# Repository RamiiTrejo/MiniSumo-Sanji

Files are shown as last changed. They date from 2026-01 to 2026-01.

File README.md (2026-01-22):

# MiniSumo-Sanji
Minisumo

 ## PLaca de Sanji
  Sanji contará con una placa hecha medida la cual puede ser alimentada con baterias de 2s-3s (LiPo), Con un microcontrolador ESP32 Embebido posee la capacidad de llevar 7 sensores, 5 de distancia y 2 de piso, con Divisores de tension en caso de trabajar con 5v, posee drivers TA6586 los cuales pueden llegar a soportar 5A de corriente pico por cada motor, tiene la opcion de agregar Pantalla Oled de 0.91 de Preferencia, ServoMotor para utilizarlo con Banderas, y Modulo de Inicio IR de Arsumo, 2 Botones de Manejo, 2 para poder cargar Programas al ESP32, y 3 Leds indicadores en caso de no querer utilizar un Display

<div align="center">
<br>
 <strong>FRONT VIEW</strong>
</div> 

<div align="center">
 <br>
 <strong>BACK VIEW</strong>
</div> 

 # 3D Sanji
minisumo v1
LATERAL MINISUMO
BACK MINISUMO

cómo se aprecia en kas imágenes, Sanji Llevara de momento 4 sensores JS40F De arsumo, también poseerá 1 par de ruedas JS2622, 2 sensores de línea QRE1113, y de momento par de Motores pololu N20 de 500RPM

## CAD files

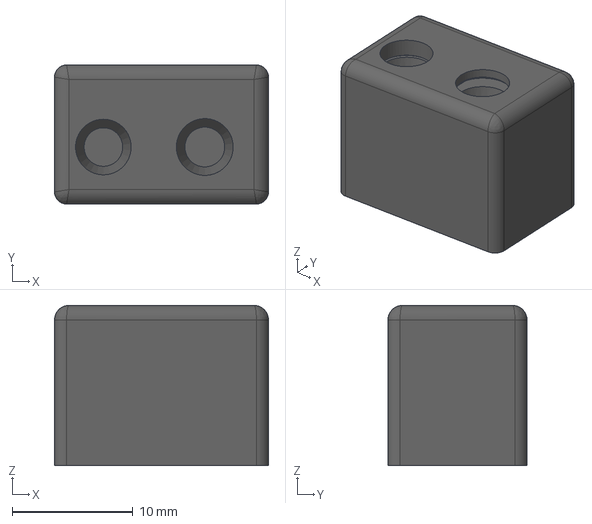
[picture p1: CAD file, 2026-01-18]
3D FILES SANJI/js40f-cad-step-jsumo.stp
17.7 x 11.5 x 13.3 mm

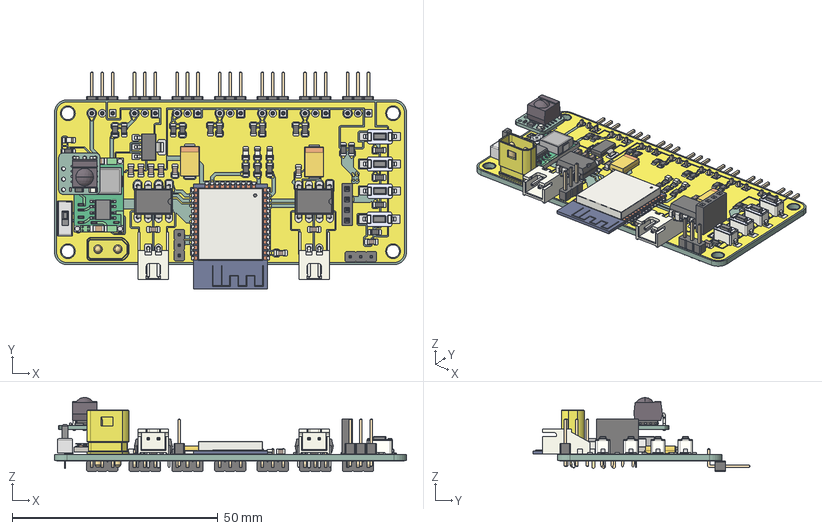
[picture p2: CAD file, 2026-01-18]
3D FILES SANJI/Sanji V1.step
85.5 x 52.7 x 18.0 mm
R_0805_2012Metric x 20
LED_0805_2012Metric x 4
PCB
C_0805_2012Metric x 10
DIP-8_W7.62mm x 2
XT30AW-M
SOT-223
JST_XH_S2B-XH-A-1_1x02_P2.50mm_Horizontal x 2
RS-032G05A3-SMRT x 4
PinHeader_1x03_P2.54mm_Vertical x 2
PinSocket_1x04_P2.54mm_Vertical
Mini360
ESP32-WROOM-32
SW_Slide-03_P2.54
CP_EIA-7343-20_Kemet-V x 2
PinHeader_1x03_P2.54mm_Horizontal x 7
Sanji V1_copper
Sanji V1_pad
Sanji V1_PCB

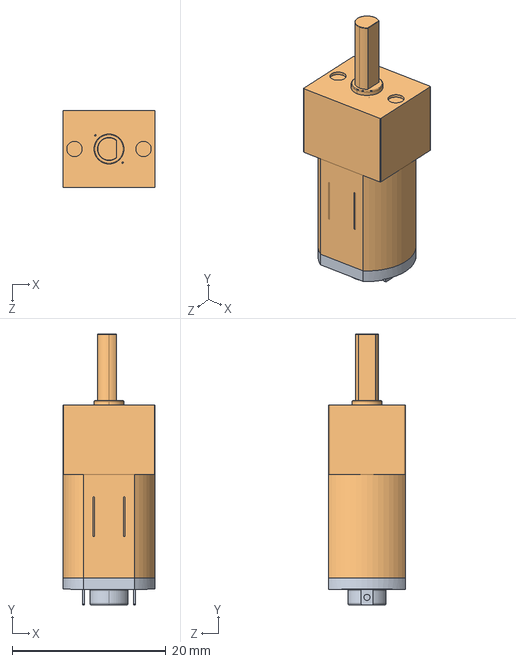
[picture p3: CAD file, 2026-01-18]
3D FILES SANJI/Pololu-Micro-Metal-Gearmotor.STEP
12.0 x 35.3 x 10.0 mm

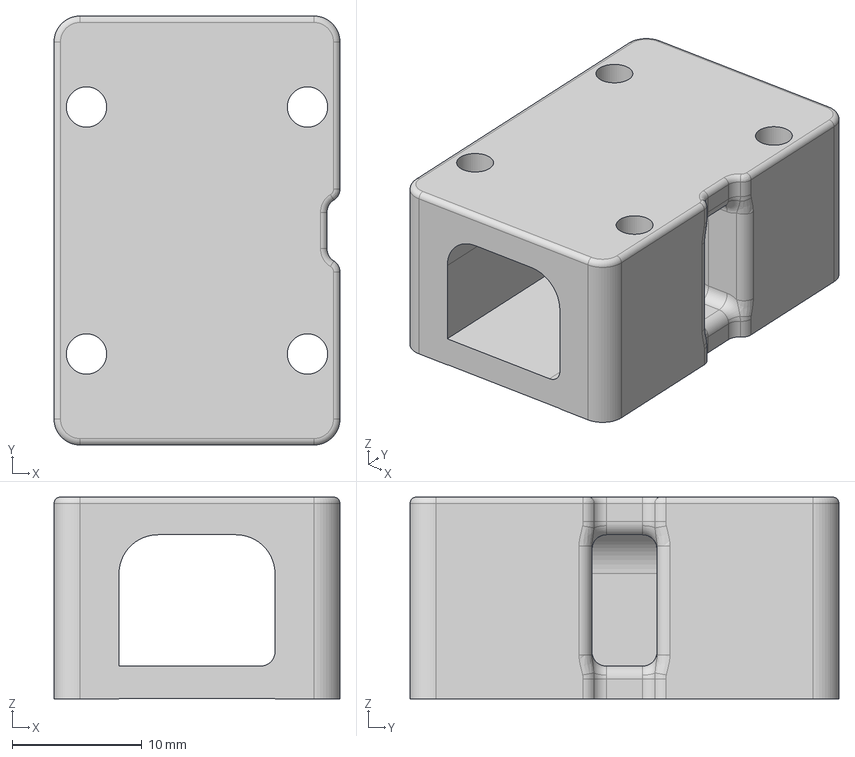
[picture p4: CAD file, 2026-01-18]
3D FILES SANJI/Bracket N20 V2.step
22.0 x 33.0 x 15.5 mm

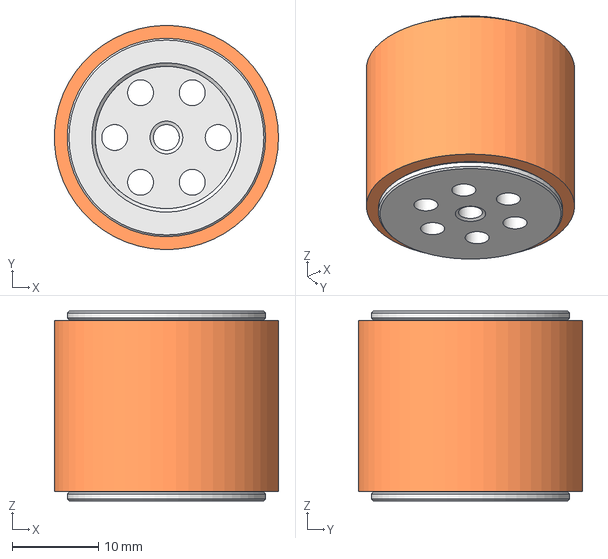
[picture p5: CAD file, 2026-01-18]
3D FILES SANJI/Rueda_JS2622.stp
26.0 x 26.0 x 22.0 mm
JS2622
Goma JS2622

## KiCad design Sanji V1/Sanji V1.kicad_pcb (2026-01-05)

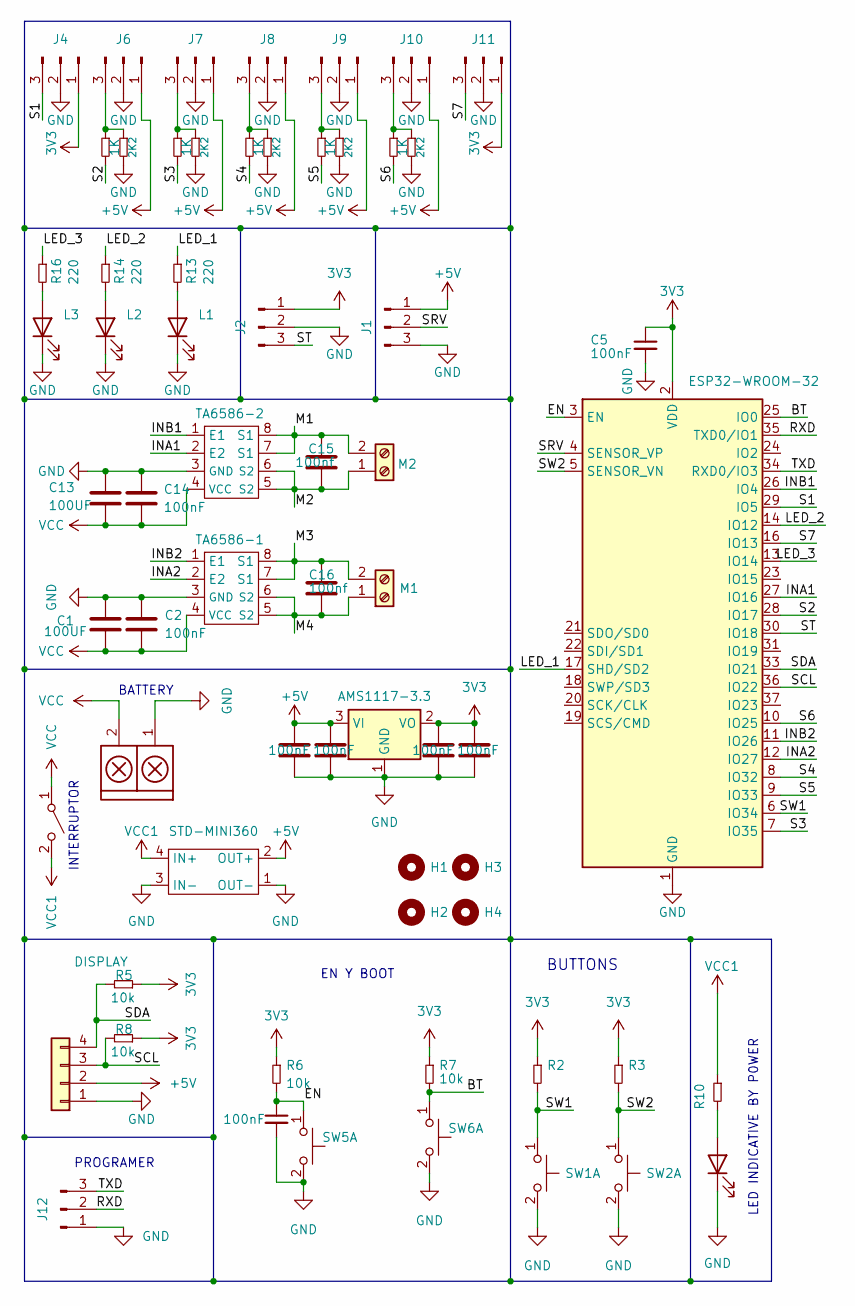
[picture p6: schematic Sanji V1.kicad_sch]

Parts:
Alimentacion1: TB_1X2; AMASS_XT30U-M_1x02_P5.0mm_Vertical
C1, C13: 100UF; CP_EIA-7343-20_Kemet-V
C2, C3, C4, C5, C6, C7, C8, C14: 100nF; C_0805_2012Metric_Pad1.18x1.45mm_HandSolder
C15, C16: 100nf; C_0805_2012Metric_Pad1.18x1.45mm_HandSolder
D2: LED; LED_0805_2012Metric_Pad1.15x1.40mm_HandSolder
H1, H2, H3, H4: MountingHole; MountingHole_3mm
J1, J2, J12: Conn_01x03_Pin; PinHeader_1x03_P2.54mm_Vertical
J3: DISPLAY; PinSocket_1x04_P2.54mm_Vertical
J4, J6, J7, J8, J9, J10, J11: Conn_01x03_Pin; PinHeader_1x03_P2.54mm_Horizontal
L1, L2, L3: LED; LED_0805_2012Metric_Pad1.15x1.40mm_HandSolder
M1: M1; JST_XH_S2B-XH-A-1_1x02_P2.50mm_Horizontal
M2: M2; JST_XH_S2B-XH-A-1_1x02_P2.50mm_Horizontal
R2, R3, R5, R6, R7, R8, R10: 10k; R_0805_2012Metric_Pad1.20x1.40mm_HandSolder
R13, R14, R16: 220; R_0805_2012Metric_Pad1.20x1.40mm_HandSolder
R15, R18, R20, R22, R24: 1K; R_0805_2012Metric_Pad1.20x1.40mm_HandSolder
R17, R19, R21, R23, R25: 2K2; R_0805_2012Metric_Pad1.20x1.40mm_HandSolder
STD-MINI360: STEP DOWN MINI 360
SW1, SW2, SW5, SW6: SW_Push_Dual_x2; SW_RS-032G05A3-SMRT
SWI1: SW_DPST_x2; PinHeader_1x03_P2.54mm_Vertical
TA6586-1, TA6586-2: DIP-8_W7.62mm
U1: AMS1117-3.3; SOT-223-3_TabPin2
U3: ESP32-WROOM-32

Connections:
3V3: C5.1, C7.1, C8.1, J2.1, J4.1, J11.1, R2.1, R3.1, R5.1, R6.1, R7.1, R8.1, U1.2 (VO), U3.2 (VDD)
+5V: C3.1, C4.1, J1.1, J3.2, J6.1, J7.1, J8.1, J9.1, J10.1, STD-MINI360.2 (OUT+), U1.3 (VI)
/BT: R7.2, SW6.1 (C), U3.25 (IO0)
/EN: C6.1, R6.2, SW5.1 (C), U3.3 (EN)
/INA1: TA6586-2.2 (E2), U3.27 (IO16)
/INA2: TA6586-1.2 (E2), U3.12 (IO27)
/INB1: TA6586-2.1 (E1), U3.26 (IO4)
/INB2: TA6586-1.1 (E1), U3.11 (IO26)
/LED_1: R13.1, U3.17 (SHD/SD2)
/LED_2: R14.1, U3.14 (IO12)
/LED_3: R16.1, U3.13 (IO14)
/M1: C15.1, M2.2, TA6586-2.7 (S1), TA6586-2.8 (S1)
/M2: C15.2, M2.1, TA6586-2.5 (S2), TA6586-2.6 (S2)
/M3: C16.1, M1.2, TA6586-1.7 (S1), TA6586-1.8 (S1)
/M4: C16.2, M1.1, TA6586-1.5 (S2), TA6586-1.6 (S2)
/RXD: J12.2, U3.35 (TXD0/IO1)
/S1: J4.3, U3.29 (IO5)
/S2: R15.2, U3.28 (IO17)
/S3: R18.2, U3.7 (IO35)
/S4: R20.2, U3.8 (IO32)
/S5: R22.2, U3.9 (IO33)
/S6: R24.2, U3.10 (IO25)
/S7: J11.3, U3.16 (IO13)
/SCL: J3.3, R8.2, U3.36 (IO22)
/SDA: J3.4, R5.2, U3.33 (IO21)
/SRV: J1.2, U3.4 (SENSOR_VP)
/ST: J2.3, U3.30 (IO18)
/SW1: R2.2, SW1.1 (C), U3.6 (IO34)
/SW2: R3.2, SW2.1 (C), U3.5 (SENSOR_VN)
/TXD: J12.3, U3.34 (RXD0/IO3)
GND: Alimentacion1.1, C1.1, C2.1, C3.2, C4.2, C5.2, C6.2, C7.2, C8.2, C13.1, C14.1, D2.1 (K), J1.3, J2.2, J3.1, J4.2, J6.2, J7.2, J8.2, J9.2, J10.2, J11.2, J12.1, L1.1 (K), L2.1 (K), L3.1 (K), R17.2, R19.2, R21.2, R23.2, R25.2, STD-MINI360.1 (OUT-), STD-MINI360.3 (IN-), SW1.2 (D), SW2.2 (D), SW5.2 (D), SW6.2 (D), TA6586-1.3 (GND), TA6586-2.3 (GND), U1.1 (GND), U3.1 (GND), U3.15 (GND), U3.38 (GND), U3.39 (GND)
unnamed: D2.2 (A), R10.2
unnamed: J6.3, R15.1, R17.1
unnamed: J7.3, R18.1, R19.1
unnamed: J8.3, R20.1, R21.1
unnamed: J9.3, R22.1, R23.1
unnamed: J10.3, R24.1, R25.1
unnamed: L1.2 (A), R13.2
unnamed: L2.2 (A), R14.2
unnamed: L3.2 (A), R16.2
VCC: Alimentacion1.2, C1.2, C2.2, C13.2, C14.2, SWI1.1 (A), TA6586-1.4 (VCC), TA6586-2.4 (VCC)
VCC1: R10.1, STD-MINI360.4 (IN+), SWI1.2 (B)

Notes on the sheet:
BUTTONS
EN Y BOOT
PROGRAMER
INTERRUPTOR
BATTERY
LED INDICATIVE BY P0WER

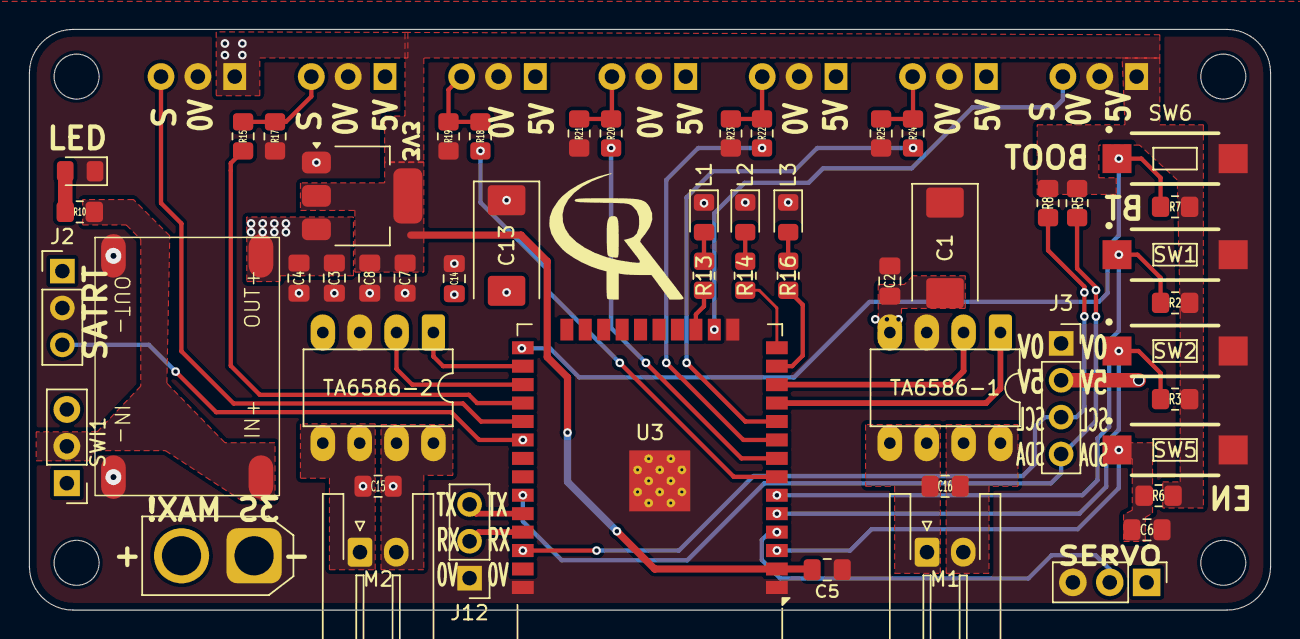
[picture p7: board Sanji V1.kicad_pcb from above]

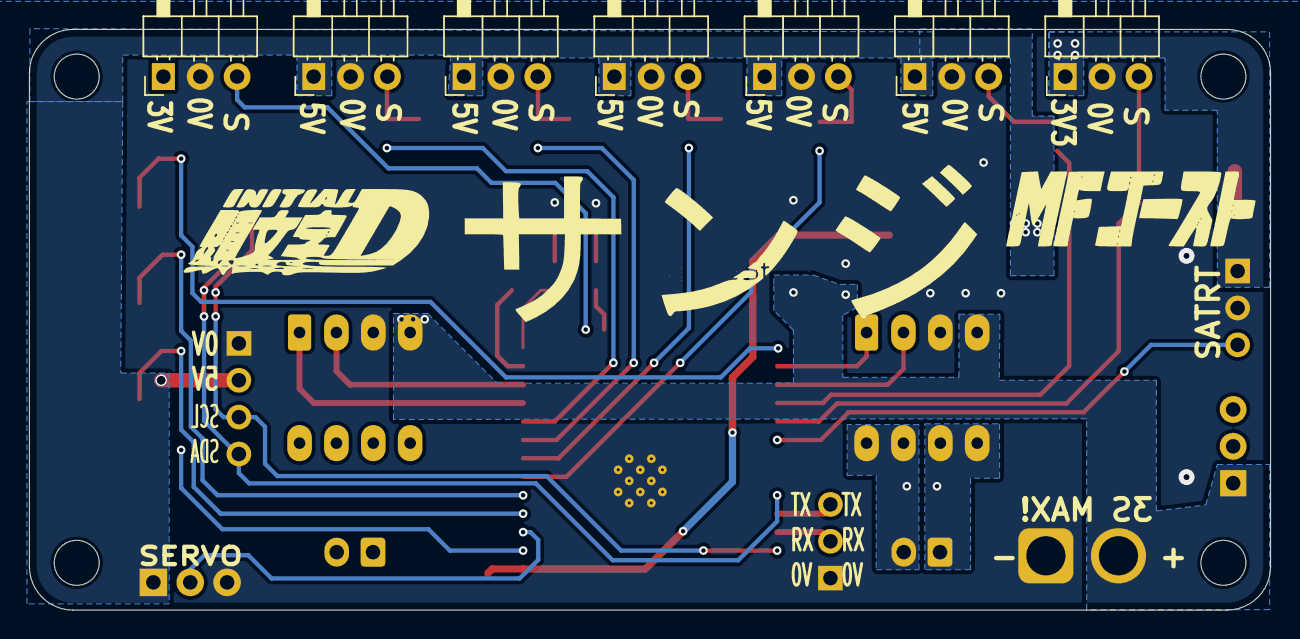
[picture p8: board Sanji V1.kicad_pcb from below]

Board: 2 copper layers, 85.5 x 40.0 mm, 64 parts (7 on the bottom side), 42 nets.
